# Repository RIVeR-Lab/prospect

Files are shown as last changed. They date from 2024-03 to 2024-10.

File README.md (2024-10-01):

# stewart_end_effector
Design and software for controlling a servo actuated stewart manipulator platform

Below is a description of and steps to run a Python script which accepts a desired pose of the Stewart platform and actuates six servos to attain that pose. The six servos must be connected via USB to the computer that is running the script, and the servos must each have a distinct ID from 1-6.

### compute_motor_angles.py:
Start a ROS service, /compute_motor_angles, which accepts the args x, y, z, psi, theta, phi (representing a desired pose of the top platform) and returns the corresponding motor angles (in radians) 
### move_to_motor_angles.py: 
A Python script which accepts the args x, y, z, psi, theta, phi (representing a desired pose of the top platform) and moves the Dynamixel servos to the required positions. Depends on the /compute_motor_angles service
### set_params.py: 
A Python script that sets the Stewart Platform parameters (i.e. crank arm length). Must be run before compute_motor_angles.py

## Example run:
1. roscore
1. rosrun set_params.py 
1. rosrun stewart_end_effector compute_motor_angles.py
1. rosrun move_to_motor_angles.py
1. rosservice call /stewart_control 5 20 95 0.1 0.2 0.3

### Troubleshooting:
1. Make sure all Dynamixel servos have unique IDs (from 1-6) through the Dynamixel Wizard ID inspection
1. move_to_motor_angles.py hardcodes information about the hardware. Double check that the information (especially the servo IDs and DEVICENAME) is correct 

### PROSPECT
Running the ur3e arm in conjunction with the kinect camera, and raster movement

ur_robot_driver can be installed from: https://github.com/UniversalRobots/Universal_Robots_ROS_Driver

ur3e_moveit_config can be installed from: http://wiki.ros.org/ur3_moveit_config

azure_kinect_ros_driver can be installed from: https://github.com/microsoft/Azure_Kinect_ROS_Driver/blob/melodic/docs/building.md

Configure host pc to be 192.168.0.86 subnet 255.255.255.0 default gateway 0.0.0.0
Configure robot pc to be 192.168.0.85

In different terminals, run the following commands: 

    roscore

    roslaunch ur_robot_driver ur3e_bringup.launch robot_ip:=192.168.0.85 kinematics_config:=$(rospack find stewart_end_effector)/config/robot_calibration.yaml

    #run rostest0 on the robot itself

    roslaunch ur3e_moveit_config moveit_planning_execution.launch

    roslaunch ur3e_moveit_config moveit_rviz.launch

    rosrun tf2_ros static_transform_publisher -0.2336 -0.152 0.774 1.57 1.57 -1.57 base_link camera_base

    roslaunch azure_kinect_ros_driver driver.launch overwrite_robot_model:=false rgb_point_cloud:=false depth_mode:=NFOV_UNBINNED 

    rosrun stewart_end_effector tof_triad.py

    roslaunch spectrometer_drivers ibsen.launch

    roslaunch stewart_end_effector master.launch

    python3 scripts/main.py

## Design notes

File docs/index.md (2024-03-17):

---
layout: default
title: Home
nav_order: 1
description: "PROSPECT"
permalink: /
---

# PROSPECT: Precision Robot Spectroscopy Exploration and Characterization Tool
**Nathaniel Hanson<sup>1,4,†,\*</sup>, Gary Lvov<sup>1,†</sup>, Vedant Rautela<sup>1</sup>, Samuel Hibbard<sup>>1</sup>, Ethan Holand<sup>1,3</sup>, Charles DiMarzio<sup>2</sup>, and Taşkın Padır<sup>1</sup>**

PROSPECT

## Abstract
Near Infrared (NIR) spectroscopy is widely used in industrial quality control and automation to test the purity and material quality of items. In this research, we propose a novel sensorized end effector and acquisition strategy to capture spectral signatures from objects and register them with a 3D point cloud. Our methodology first takes a 3D scan of an object generated by a time-of-flight depth camera and decomposes the object into a series of planned viewpoints covering the surface. We generate motion plans for a robot manipulator and end-effector to visit these viewpoints while maintaining a fixed distance and surface normal to ensure maximal spectral signal quality enabled by the spherical motion of the end-effector. By continuously acquiring surface reflectance values as the end-effector scans the target object, the autonomous system develops a four-dimensional model of the target object: position in an **R<sup>3</sup>** coordinate frame, and a wavelength vector denoting the associated spectral signature. We demonstrate this system in building spectral-spatial object profiles of increasingly complex geometries. As a point of comparison, we show our proposed system and spectral acquisition planning yields more consistent signal signals than naïve point scanning strategies for capturing spectral information over complex surface geometries. Our work represents a significant step towards high-resolution spectral-spatial sensor fusion for automated quality assessment.

- *†Equal Contribution; \*Corresponding author*
- *<sup>1</sup>Institute for Experiential Robotics*
- *<sup>2</sup>Electrical and Computer Engineering Department, Northeastern University, Boston, Massachusetts, USA.*
- *<sup>3</sup>Robotics Institute, Carnegie Mellon University, Pittsburgh, Pennsylvania, USA.*
- *<sup>4</sup>Lincoln Laboratory, Massachusetts Institute of Technology, Lexington, Massachusetts, USA.*

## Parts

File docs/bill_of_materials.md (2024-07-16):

---
layout: default
title: Bill of Materials
nav_order: 2
description: "Bill of materials for PROSPECT"
---

| BOM # | DESCRIPTION | QTY. | SUPPLIER | MATERIAL | PART NUMBER |
| ----- | --- | ---- | --- | --- | --- |
| 1 | [Bottom Platform](https://github.com/RIVeR-Lab/prospect/blob/main/CAD/STL/Bottom_Platform.STL) | 1 | CUSTOM PRINTED | ONYX | |
| 2 | [Crank Arm](https://github.com/RIVeR-Lab/prospect/blob/main/CAD/STL/Crank_Arm.STL) | 6 | CUSTOM PRINTED | ONYX | |
| 3 | [UR3 Adapter Plate](https://github.com/RIVeR-Lab/prospect/blob/main/CAD/STL/UR3_Adapter_Plate.STL) | 1 | CUSTOM PRINTED | ONYX | |
| 4 | [Top Platform](https://github.com/RIVeR-Lab/prospect/blob/main/CAD/STL/Top_Platform.STL) | 1 | CUSTOM PRINTED | ONYX | |
| 5 | [Top Platform Bottom Cover](https://github.com/RIVeR-Lab/prospect/blob/main/CAD/STL/Top_Platform_Bottom_Cover.STL) | 1 | CUSTOM PRINTED | ONYX | |
| 6 | [Electronics Enclosure](https://github.com/RIVeR-Lab/prospect/blob/main/CAD/STL/Electronics_Enclosure.STL) | 1 | CUSTOM PRINTED | ONYX | |
| 7 | [Electronics Lid](https://github.com/RIVeR-Lab/prospect/blob/main/CAD/STL/Electronics_Lid.STL) | 1 | CUSTOM PRINTED | ONYX | |
| 8 | [Electronics Enclosure Adapter](https://github.com/RIVeR-Lab/prospect/blob/main/CAD/STL/Electronics_Enclosure_Adapter.STL) | 3 | CUSTOM PRINTED | ONYX | |
| 9 | [Dynamixel XL,XC-330](https://www.robotis.us/dynamixel-xl330-m288-t/) | 6 | ROBOTIS | | XL330-M288-T |
| 10 | [Robotis U2D2](https://www.robotis.us/u2d2/) | 1 | ROBOTIS | | 902-0132-000 |
| 11 | [SMPS2Dynamixel](https://www.robotis.us/smps2dynamixel/) | 1 | ROBOTIS | | 902-0034-000 |
| 12 | [Adafruit QT Py-SAMD21](https://www.adafruit.com/product/4600) | 1 | Adafruit | | SAMD21 |
| 13 | [VL53L4CD TOF Sensor](https://www.adafruit.com/product/5396) | 3 | Adafruit | | VL53L4CD |
| 14 | [LIGHT BULBS](https://internationallight.com/instrumentation-and-sensor-light-sources/1896-t1-miniature-incandescent-ndir-lamp) | 3 | International Light Technologies | | 1150-9A LAMP 5V 115mA |
| 15 | [MOSFET](https://www.amazon.com/EEEEE-Transistors-Transistor-Assortment-Compartment/dp/B095NMT2SL) | 1 | Amazon | | BC517 |
| 16 | [Brass Screw-to-Expand Inserts](https://www.mcmaster.com/94510A030/) | 12 | McMaster-Carr | | 94510A030 |
| 17 | [Right Handed Oil-Embedded Ball Joint](https://www.mcmaster.com/6072K35/) | 6 | McMaster-Carr | | 6072K35 |
| 18 | [Left Handed Oil-Embedded Ball Joint](https://www.mcmaster.com/6072K351/) | 6 | McMaster-Carr | | 6072K351 |
| 19 | [Aluminum Unthreaded Spacer](https://www.mcmaster.com/92510A562/) | 12 | McMaster-Carr | | 92510A562 |
| 20 | [Aluminum Turnbuckle Connecting Rod](https://www.mcmaster.com/8420K171/) | 6 | McMaster-Carr | | 8420K171 |
| 21 | [Thread-Forming Screws M2x8](https://www.mcmaster.com/90380A327/) | 18 | McMaster-Carr | | 90380A327 |
| 22 | [Thread-Forming Screws M2x6](https://www.mcmaster.com/90380A326/) | 34 | McMaster-Carr | | 90380A326 |
| 23 | [Socket Head Cap Screw, M2x14](https://www.mcmaster.com/91290A045/) | 3 | McMaster-Carr | | 91290A045 |

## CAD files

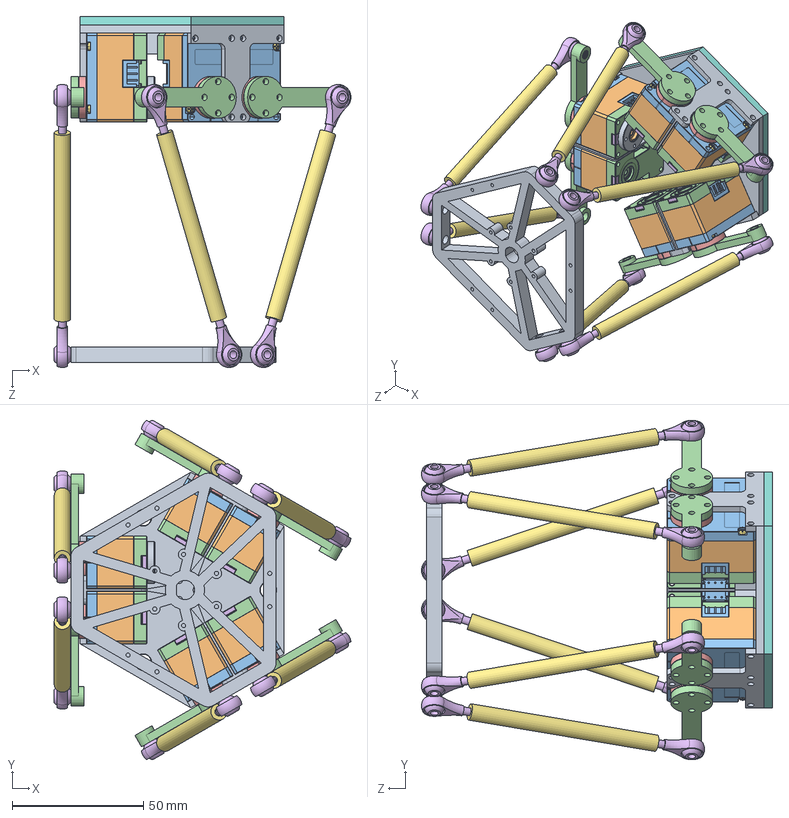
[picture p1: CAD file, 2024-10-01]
matlab/stewart_cad.SLDASM
113.2 x 129.3 x 133.8 mm
Bottom Platform_42023
DC15_A01_CASE_M_DUMMY.stp x 6
DC15_A01_CASE_F_DUMMY.stp x 6
DC15_A01_CASE_B_DUMMY.stp x 6
DC15_A01_HORN_DUMMY.stp x 6
DC15_A01_LED_CAP2_DUMMY.stp x 6
PHS_1_7X20_5_DC10.stp x 24
BTS2_M2_6X8.stp x 6
B3B-EH.stp x 12
SP, Crank Arm_42023 x 6
94510A030_Brass Screw-to-Expand Inserts_42023
59935K11_Ball Joint Rod End_42023 x 12
7415N11_Internally Threaded Connecting Rod_42023 x 6
Adapter Plate_42023
Top Platform 1_42023

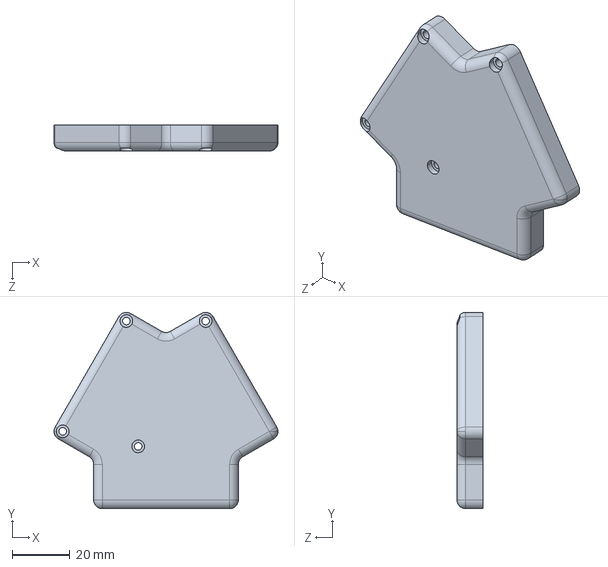
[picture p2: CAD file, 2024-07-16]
CAD/STEP/Electronics_Lid.STEP
77.4 x 67.8 x 9.00 mm

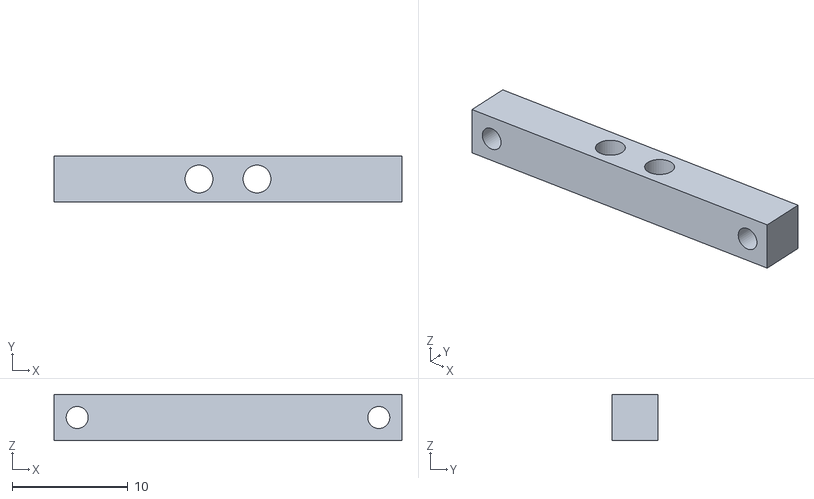
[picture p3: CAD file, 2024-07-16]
CAD/STL/Electronics_Enclosure_Adapter.STL
30.0 x 4.00 x 4.00

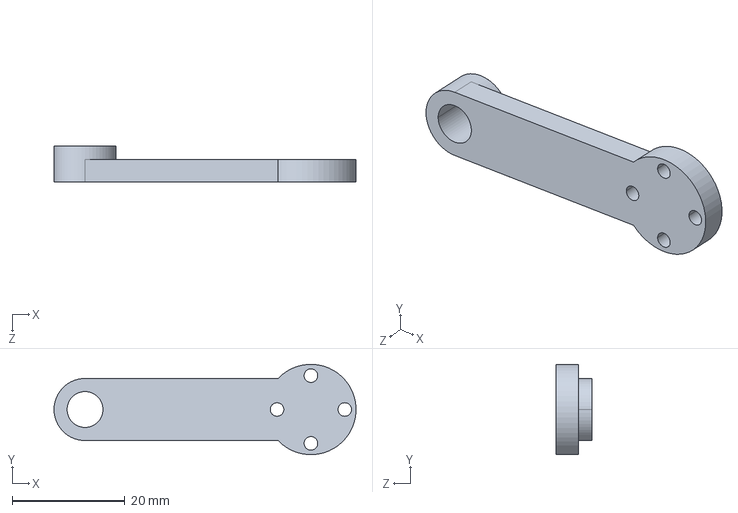
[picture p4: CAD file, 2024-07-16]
CAD/STEP/Crank_Arm.STEP
53.5 x 16.0 x 6.35 mm

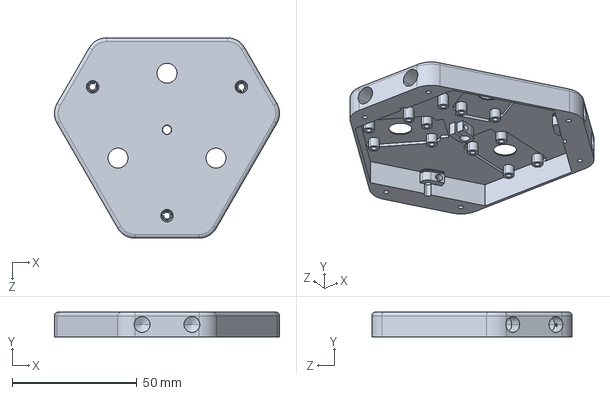
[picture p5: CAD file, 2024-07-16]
CAD/STEP/Top_Platform.STEP
90.3 x 10.0 x 80.4 mm

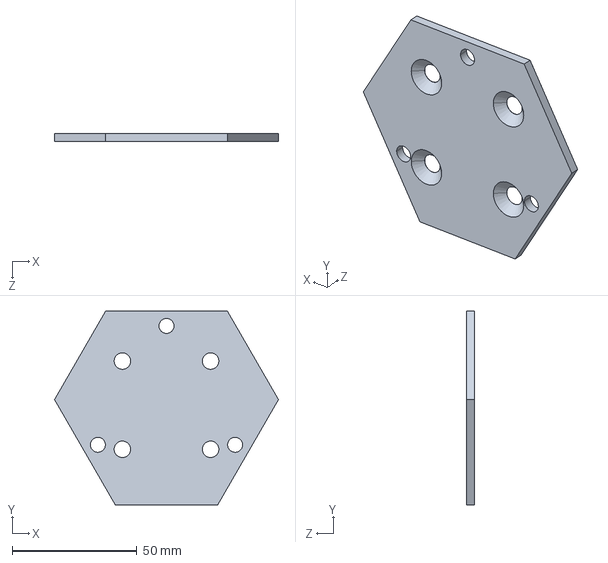
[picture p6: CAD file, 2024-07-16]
CAD/STEP/UR3_Adapter_Plate.STEP
89.8 x 77.8 x 3.30 mm

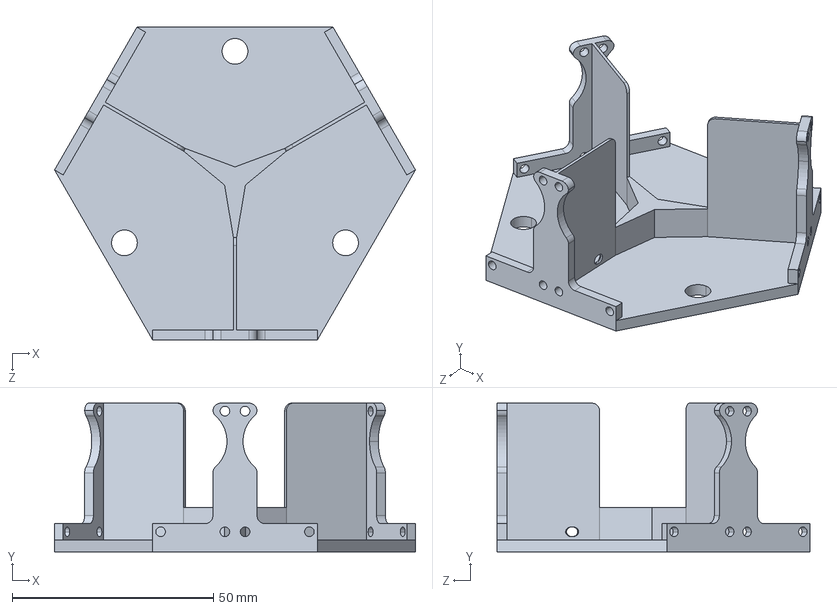
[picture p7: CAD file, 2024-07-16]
CAD/STEP/Bottom_Platform.STEP
89.8 x 37.0 x 77.8 mm

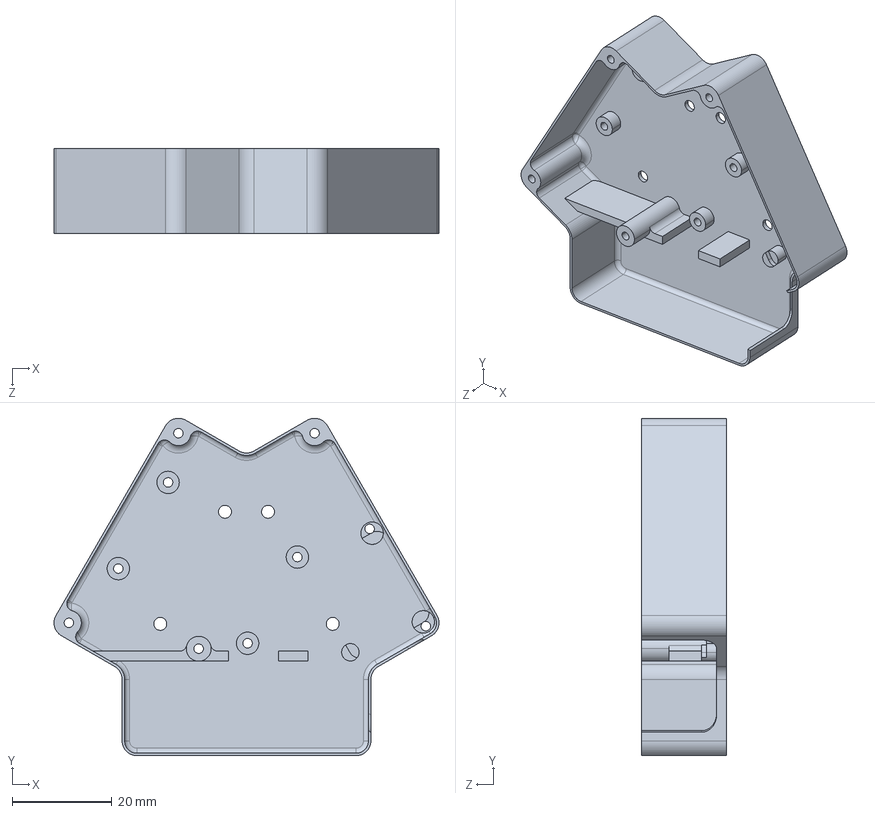
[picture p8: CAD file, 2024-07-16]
CAD/STEP/Electronics_Enclosure.STEP
77.4 x 67.8 x 17.1 mm

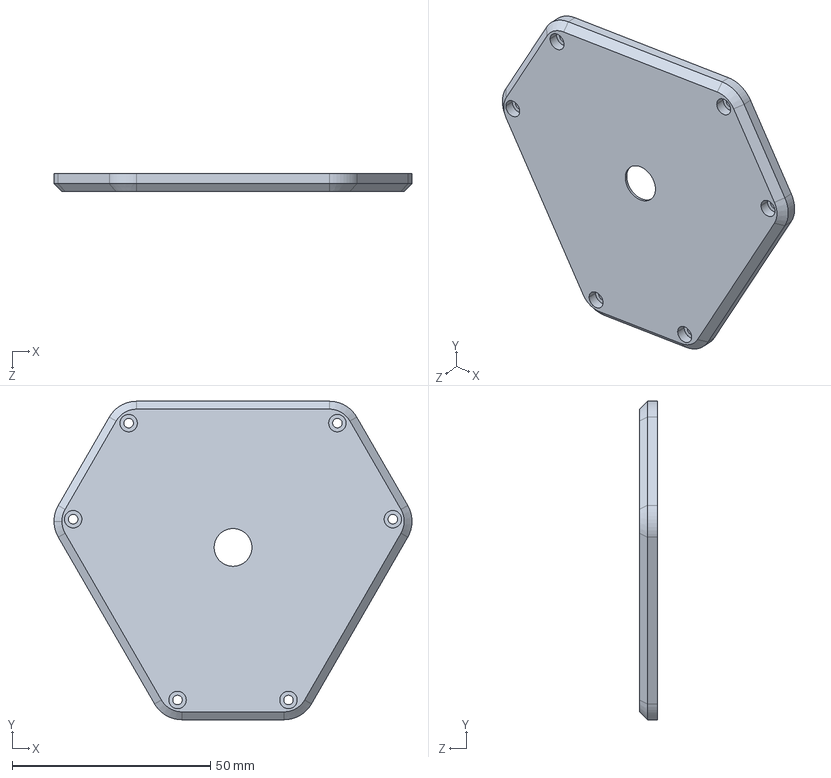
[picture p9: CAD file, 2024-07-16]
CAD/STEP/Top_Platform_Bottom_Cover.STEP
90.4 x 80.4 x 4.60 mm

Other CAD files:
CAD/STL/Bottom_Platform.STL
CAD/STL/Crank_Arm.STL
CAD/STL/Electronics_Enclosure.STL
CAD/STL/Electronics_Lid.STL
CAD/STL/Top_Platform.STL
CAD/STL/Top_Platform_Bottom_Cover.STL
CAD/STL/UR3_Adapter_Plate.STL

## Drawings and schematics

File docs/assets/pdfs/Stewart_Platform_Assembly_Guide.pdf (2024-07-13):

## 1: Final Assembled Model

4

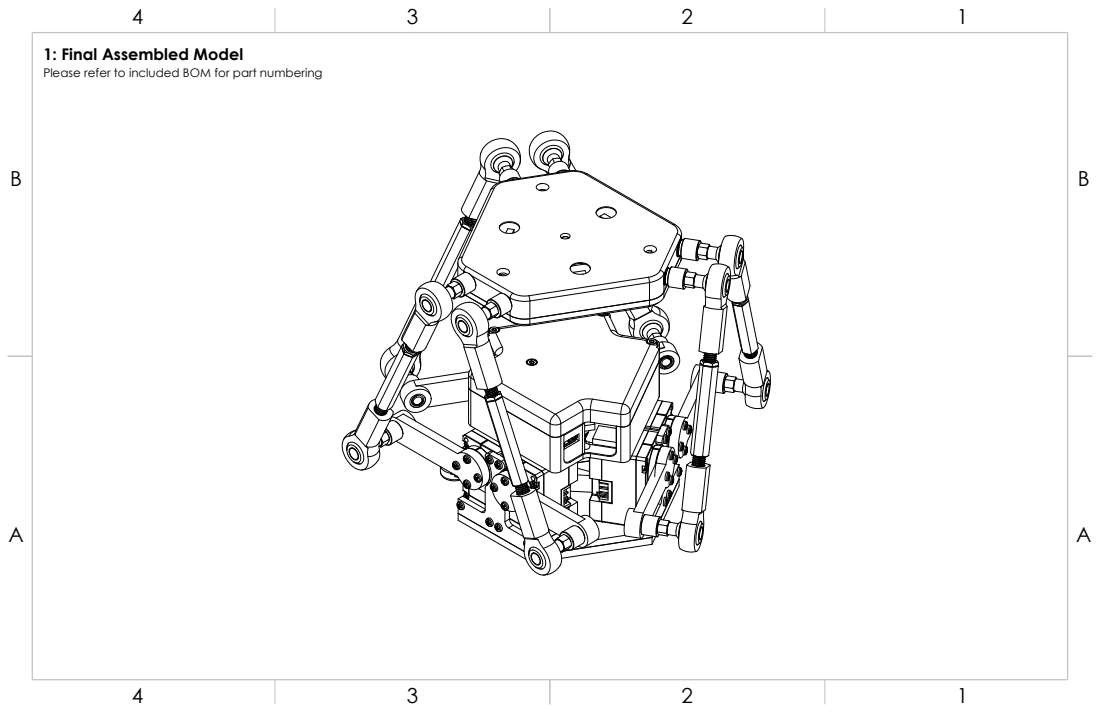
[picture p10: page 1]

Please refer to included BOM for part numbering

B B

## 2: Base Assembly

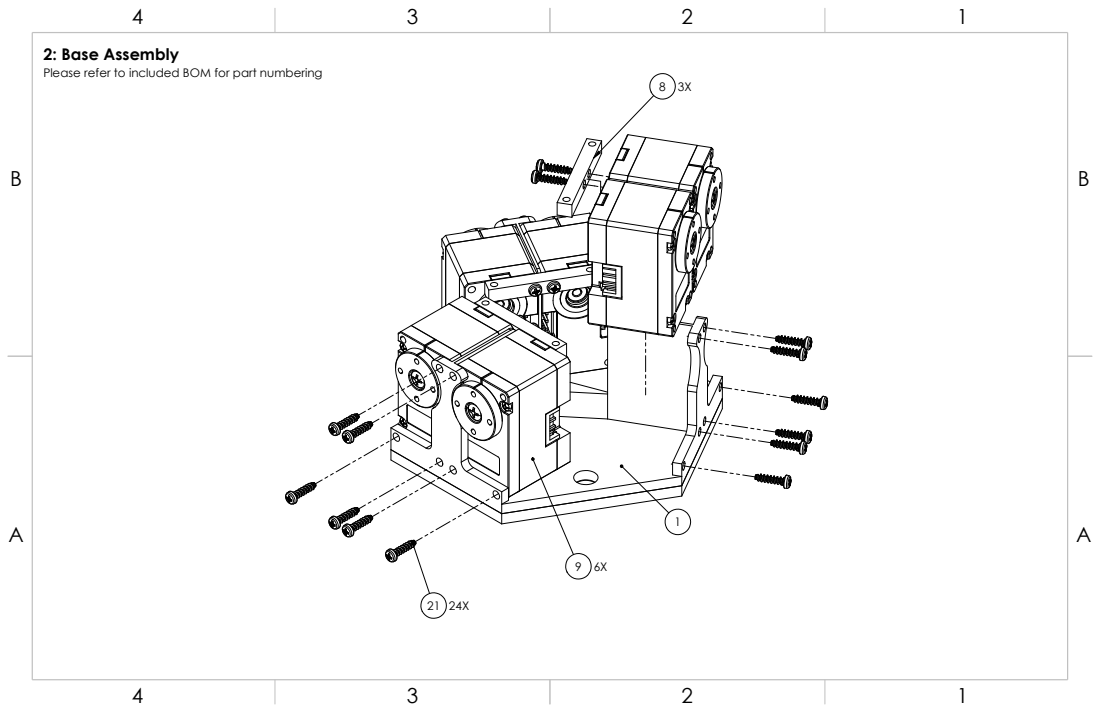
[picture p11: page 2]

Please refer to included BOM for part numbering

## 3: Crank Arms

B B

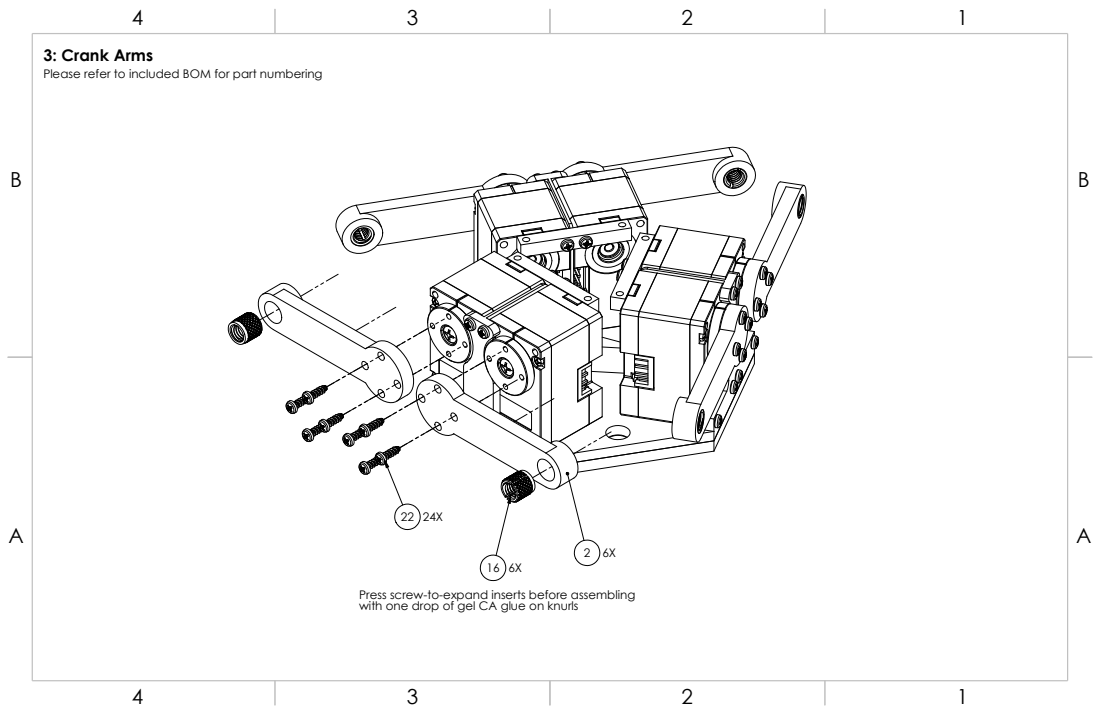
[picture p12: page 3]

Please refer to included BOM for part numbering

Press screw-to-expand inserts before assembling
with one drop of gel CA glue on knurls

B B

## 4: Electronics

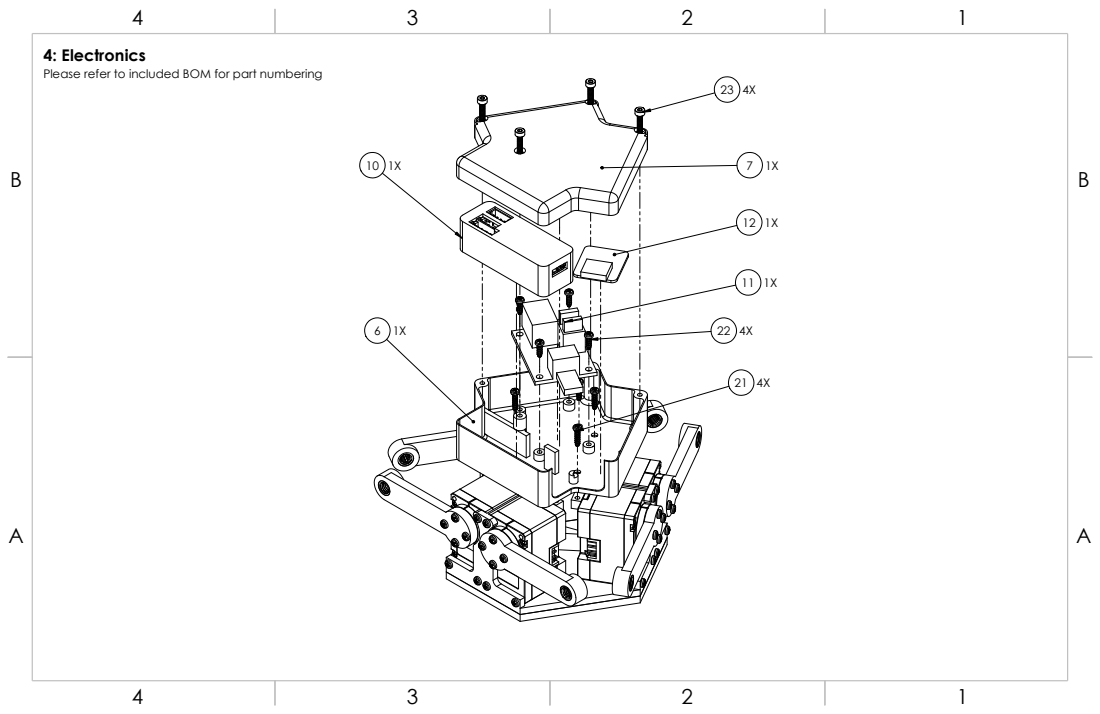
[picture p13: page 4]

Please refer to included BOM for part numbering

B B

## 5: Top Platform

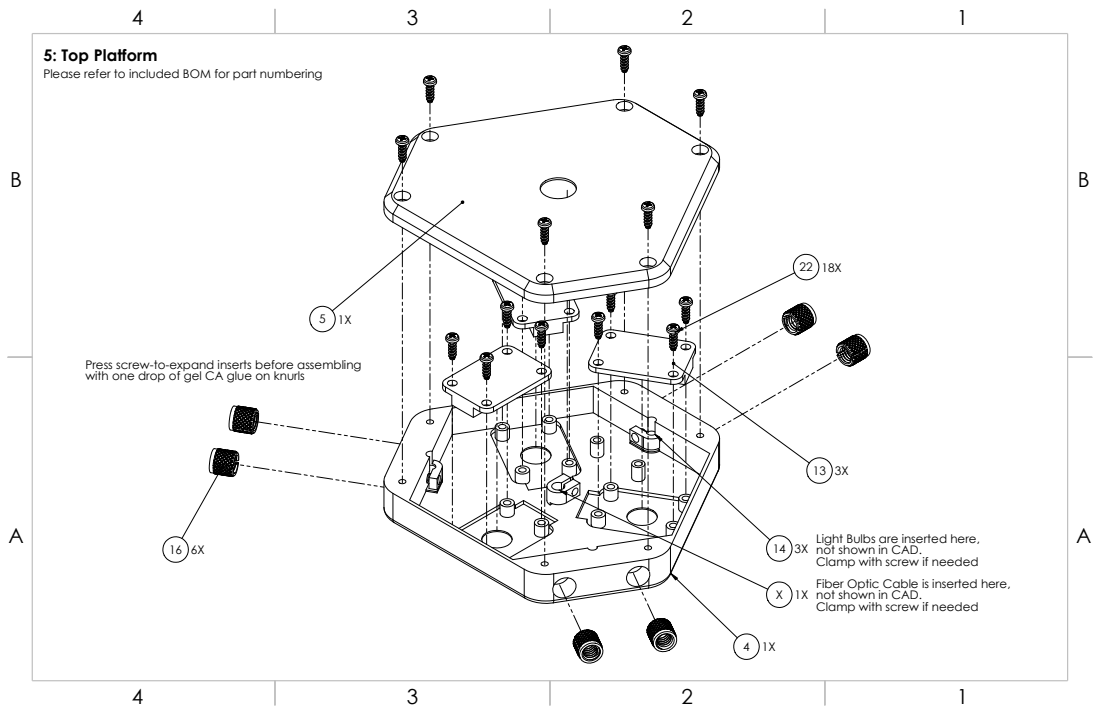
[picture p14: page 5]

Please refer to included BOM for part numbering

Press screw-to-expand inserts before assembling
with one drop of gel CA glue on knurls

Light Bulbs are inserted here,
not shown in CAD.
Clamp with screw if needed
Fiber Optic Cable is inserted here,

## 6: Links

B B

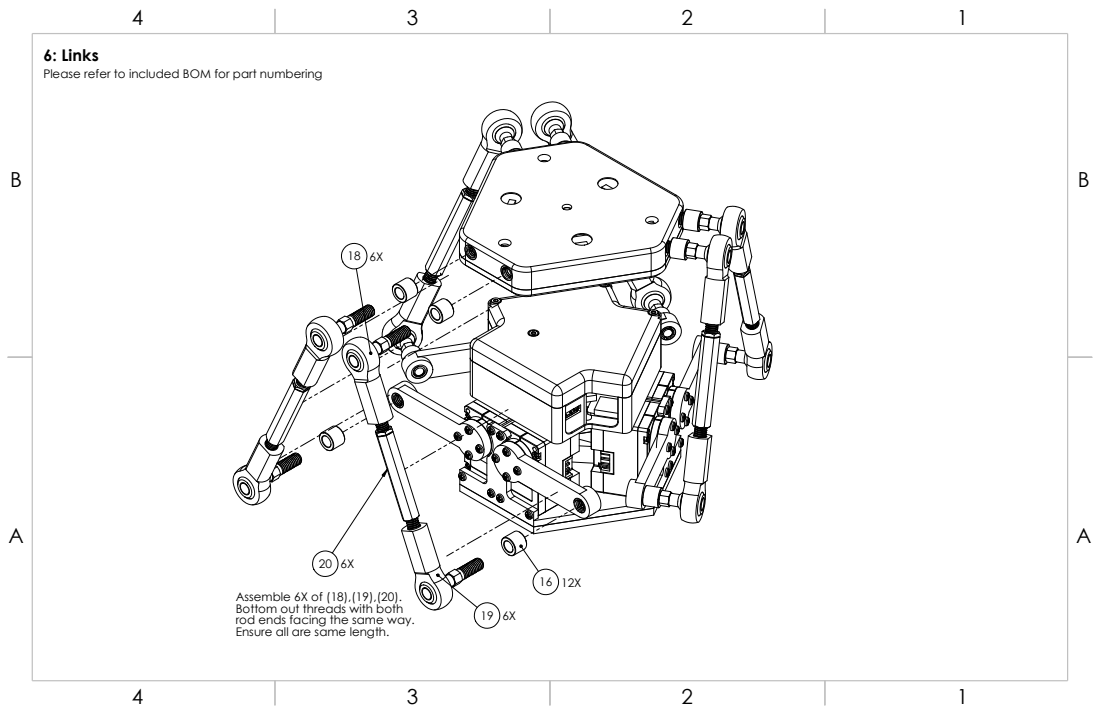
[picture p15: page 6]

Please refer to included BOM for part numbering

Assemble 6X of (18),(19),(20).
Bottom out threads with both
rod ends facing the same way.
Ensure all are same length.

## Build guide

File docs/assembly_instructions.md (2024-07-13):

---
layout: default
title: Assembly Instructions
nav_order: 3
description: "Assembly instructions for PROSPECT"
---

<iframe src="{{ site.baseurl }}/assets/pdfs/Stewart_Platform_Assembly_Guide.pdf" width="100%" height="600px">
    This browser does not support PDFs. Please download the PDF to view it: <a href="{{ site.baseurl }}/assets/pdfs/Stewart_Platform_Assembly_Guide.pdf">Download PDF</a>.
</iframe>

[Download PDF](assets/pdfs/Stewart_Platform_Assembly_Guide.pdf)

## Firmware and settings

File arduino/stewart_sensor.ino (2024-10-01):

#include <Wire.h>
#include "SparkFun_VL53L1X.h"

#define WIRE Wire
#define TCAADDR 0x70
//Optional interrupt and shutdown pins.
#define SHUTDOWN_PIN 2
#define INTERRUPT_PIN 3

SFEVL53L1X distanceSensor1;
SFEVL53L1X distanceSensor2;
SFEVL53L1X distanceSensor3;

// Helper function for changing TCA output channel
void tcaselect(uint8_t channel) {
  if (channel > 7) return;
  WIRE.beginTransmission(TCAADDR);
  WIRE.write(1 << channel);
  WIRE.endTransmission();  
}

void setup() {
  Serial.begin(9600);
  
  while (!Serial) {
     delay(10);
  }
  Serial.println("\nI2C Scanner");
  
  WIRE.begin();
  tcaselect(1);
  if (distanceSensor1.init() == false)
    Serial.println("Sensor #1 online!");
   tcaselect(6);
  if (distanceSensor2.init() == false)
    Serial.println("Sensor #2 online!"); 
  tcaselect(7);
  if (distanceSensor3.init() == false)
    Serial.println("Sensor #3 online!"); 
  pinMode(A0, OUTPUT);    // sets the digital pin 13 as output
  digitalWrite(A0, HIGH); // sets the digital pin 13 on
}


void find_devices() {
  byte error, address;
  int nDevices;
  Serial.println("Scanning...");
  nDevices = 0;
  for(address = 1; address < 127; address++ ) 
  {
    // The i2c_scanner uses the return value of
    // the Write.endTransmisstion to see if
    // a device did acknowledge to the address.
    WIRE.beginTransmission(address);
    error = WIRE.endTransmission();

    if (error == 0)
    {
      Serial.print("I2C device found at address 0x");
      if (address<16) 
        Serial.print("0");
      Serial.print(address,HEX);
      Serial.println("  !");

      nDevices++;
    }
    else if (error==4) 
    {
      Serial.print("Unknown error at address 0x");
      if (address<16) 
        Serial.print("0");
      Serial.println(address,HEX);
    }    
  }
  if (nDevices == 0)
    Serial.println("No I2C devices found\n");
  else
    Serial.println("done\n");
}

void readSerial() {
  String str = Serial.readString();
  // Check string is non-empty
  if (str.length() < 3){
    return;
  }
  // Set light value
  if (str.indexOf("light_power") > -1) {
    // Set light equal to the power value
    int offset = 12; // Number of characters until useful data begins
    String command = str.substring(offset);
    command.trim();
    if (command.equals("ON")) {
      digitalWrite(A0, LOW); 
    } else if (command.equals("OFF")) {
      digitalWrite(A0, HIGH); 
    }
    return;
  }
//  // Set integration time
//  if (str.indexOf("integration_time") > -1) {
//    // Extract the integration time to use
//    // Set light equal to the power value
//    int offset = 16; // Number of characters until useful data begins
//    String command = str.substring(offset);
//    command.trim();
//    // Convert string to integer value
//    int newTime = command.toInt();
//    delayTime = newTime;
//  }
}

void loop() {
//  Serial.println("Checking index 0");
  tcaselect(1);
  distanceSensor1.startRanging(); //Write configuration bytes to initiate measurement
  int distance1 = distanceSensor1.getDistance(); //Get the result of the measurement from the sensor
  distanceSensor1.stopRanging();
//  Serial.println("Checking index 1");
  tcaselect(6);
  distanceSensor2.startRanging(); //Write configuration bytes to initiate measurement
  int distance2 = distanceSensor2.getDistance(); //Get the result of the measurement from the sensor
  distanceSensor2.stopRanging();
//  Serial.println("Checking index 2");
  tcaselect(7);
  distanceSensor3.startRanging(); //Write configuration bytes to initiate measurement
  int distance3 = distanceSensor3.getDistance(); //Get the result of the measurement from the sensor
  distanceSensor3.stopRanging();
  Serial.print("Distance 1 (mm): ");
  Serial.print(distance1);
  Serial.print(", Distance 2 (mm): ");
  Serial.print(distance2);
  Serial.print(", Distance 3 (mm): ");
  Serial.print(distance3);
  Serial.println();
//  digitalWrite(A0, HIGH); // sets the digital pin 13 on
  //delay(100);          // wait 10 milliseconds for the next scan
//  digitalWrite(A0, LOW); // sets the digital pin 13 on
  //delay(100);          // wait 10 milliseconds for the next scan
  delay(10);
  readSerial();

}

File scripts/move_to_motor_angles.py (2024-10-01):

#!/usr/bin/env python3

import numpy as np
import os
import rospy
import sys
from threading import Lock
from std_msgs.msg import Float32MultiArray
from stewart_end_effector.srv import StewartControl, ComputeMotorAngles, ComputeMotorAnglesResponse
from compute_motor_angles import normalize_motor_angles_zero_twopi, normalize_motor_angles_pi_minus_pi
from stewart_end_effector.srv import StewartControl, StewartControlRequest, StewartControlResponse


if os.name == 'nt':
    import msvcrt
    def getch():
        return msvcrt.getch().decode()
else:
    import sys, tty, termios
    fd = sys.stdin.fileno()
    old_settings = termios.tcgetattr(fd)
    def getch():
        try:
            tty.setraw(sys.stdin.fileno())
            ch = sys.stdin.read(1)
        finally:
            termios.tcsetattr(fd, termios.TCSADRAIN, old_settings)
        return ch


from dynamixel_sdk.port_handler import PortHandler # goes into the port_handler.py file and imports the class PortHandler
from dynamixel_sdk.packet_handler import PacketHandler # does the same as the previous line but PacketHandler is a function
from dynamixel_sdk.group_sync_write import GroupSyncWrite
from dynamixel_sdk.group_sync_read import GroupSyncRead
from dynamixel_sdk.robotis_def import *
import dynamixel_sdk as dxl

#********* DYNAMIXEL Model definition *********
#***** (Use only one definition at a time) *****
MY_DXL = 'X_SERIES'       # X330 (5.0 V recommended), X430, X540, 2X430
# Control table address
if MY_DXL == 'X_SERIES' or MY_DXL == 'MX_SERIES':
    ADDR_TORQUE_ENABLE          = 64
    ADDR_GOAL_POSITION          = 116
    LEN_GOAL_POSITION           = 4         # Data Byte Length
    ADDR_PRESENT_POSITION       = 132
    LEN_PRESENT_POSITION        = 4         # Data Byte Length
    ADDR_HARDWARE_ERROR              = 70
    LEN_HARDWARE_ERROR          = 1
    DXL_MINIMUM_POSITION_VALUE  = 0         # Refer to the Minimum Position Limit of product eManual
    DXL_MAXIMUM_POSITION_VALUE  = 4095      # Refer to the Maximum Position Limit of product eManual
    BAUDRATE                    = 57600

# DYNAMIXEL Protocol Version (1.0 / 2.0)
# https://emanual.robotis.com/docs/en/dxl/protocol2/
PROTOCOL_VERSION            = 2.0

# Make sure that each DYNAMIXEL ID should have unique ID.
DXL1_ID                     = 1                 # Dynamixel#1 ID : 1
DXL2_ID                     = 2                 # Dynamixel#1 ID : 2
DXL3_ID                     = 3                 # Dynamixel#1 ID : 3
DXL4_ID                     = 4                 # Dynamixel#1 ID : 4
DXL5_ID                     = 5                 # Dynamixel#1 ID : 5
DXL6_ID                     = 6                 # Dynamixel#1 ID : 6

DXL_IDS = [DXL1_ID, DXL2_ID, DXL3_ID, DXL4_ID, DXL5_ID, DXL6_ID]

# Use the actual port assigned to the U2D2.
# ex) Windows: "COM*", Linux: "/dev/ttyUSB*", Mac: "/dev/tty.usbserial-*"
DEVICENAME                  = '/dev/output/stewart-motor'

TORQUE_ENABLE               = 1                 # Value for enabling the torque
TORQUE_DISABLE              = 0                 # Value for disabling the torque
DXL_MOVING_STATUS_THRESHOLD = 20                # Dynamixel moving status threshold

DEGREE_TO_POSITION_VALUE = (DXL_MAXIMUM_POSITION_VALUE - DXL_MINIMUM_POSITION_VALUE)/360.0


class MoveMotorAngles():
    def __init__(self):
        # Initialize PortHandler instance
        # Set the port path
        # Get methods and members of PortHandlerLinux or PortHandlerWindows
        self.portHandler = PortHandler(DEVICENAME)

        # Initialize PacketHandler instance
        # Set the protocol version
        # Get methods and members of Protocol1PacketHandler or Protocol2PacketHandler
        self.packetHandler = PacketHandler(PROTOCOL_VERSION)

        # Initialize GroupSyncWrite instance
        self.groupSyncWrite = GroupSyncWrite(self.portHandler, self.packetHandler, ADDR_GOAL_POSITION, LEN_GOAL_POSITION)

        # Initialize GroupSyncRead instance for Present Position
        self.groupSyncRead = GroupSyncRead(self.portHandler, self.packetHandler, ADDR_PRESENT_POSITION, LEN_PRESENT_POSITION)
        self.groupSyncReadAlarm = GroupSyncRead(self.portHandler, self.packetHandler, ADDR_HARDWARE_ERROR, LEN_HARDWARE_ERROR)

        self.pub = rospy.Publisher('actual_motor_positions', Float32MultiArray, queue_size=1)
        self.pub_srv_lock = Lock()

    
    def initialize(self):
        # Open port
        if self.portHandler.openPort():
            print("Succeeded to open the port")
        else:
            print("Failed to open the port")
            print("Press any key to terminate...")
            getch()
            quit()

        # Set port baudrate
        if self.portHandler.setBaudRate(BAUDRATE):
            print("Succeeded to change the baudrate")
        else:
            print("Failed to change the baudrate")
            print("Press any key to terminate...")
            getch()
            quit()

    
    def zero_platform(self):
        '''
        Zero the platform to start
        '''
        rospy.sleep(3)
        cmd = StewartControl()
        cmd.x, cmd.y, cmd.z, cmd.psi, cmd.theta, cmd.phi = 0, 0, 100, 0, 0, 0
        self.compute_motor_angles_client(cmd)

    # Initialize each of the servos with certain parameters
    def boot_servo(self, dxl_id):
        # TODO: ensure that torque does not need to be enabled when booting servos since auto-enable was set in the Dynamixel Wizard
        # Enable torques for each of the Dynamixels
        dxl_comm_result, dxl_error = self.packetHandler.write1ByteTxRx(self.portHandler, dxl_id, ADDR_TORQUE_ENABLE, TORQUE_ENABLE)
        if dxl_comm_result != COMM_SUCCESS:
            print("NO COMM SUCCESS")
            print(dxl_comm_result)
            print("%s" % self.packetHandler.getTxRxResult(dxl_comm_result))
        elif dxl_error != 0:
            print("DXL ERROR")
            print("%s" % self.packetHandler.getRxPacketError(dxl_error))
        else:
            print("Dynamixel#%d has been successfully connected" % dxl_id)

        ADDR_PROFILE_VELOCITY = 112
        DESIRED_MAX_VELOCITY = 30
        self.set_servo_param(dxl_id, 'profile velocity', 4, ADDR_PROFILE_VELOCITY, DESIRED_MAX_VELOCITY)

        ADDR_POSITION_D_GAIN = 80
        DESIRED_POSITION_D_GAIN = 0
        self.set_servo_param(dxl_id, 'position D gain', 2, ADDR_POSITION_D_GAIN, DESIRED_POSITION_D_GAIN)

        ADDR_POSITION_I_GAIN = 82
        DESIRED_POSITION_I_GAIN = 250
        self.set_servo_param(dxl_id, 'position I gain', 2, ADDR_POSITION_I_GAIN, DESIRED_POSITION_I_GAIN)

        ADDR_POSITION_P_GAIN = 84
        DESIRED_POSITION_P_GAIN = 500
        self.set_servo_param(dxl_id, 'position P gain', 2, ADDR_POSITION_P_GAIN, DESIRED_POSITION_P_GAIN)
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

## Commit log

2024-07-02 Added CAD files
    [Bottom_Platform.STL, Crank_Arm.STL, Electronics_Enclosure_Adapter.STL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]
2024-07-02 Renamed STL Files and added links to BOM
    [Stewart_Electronics_Enclosure_Lid.STL, Top_Platform_Bottom_Cover.STL]
2024-07-02 Update bill_of_materials.md
    Corrected STL Links
2024-07-13 try to add embed assembly instructions pdf
2024-07-14 Update bill_of_materials.md
    Add BOM # and reformat links
2024-07-16 Added STEP models and updated STLs
    [Bottom_Platform.STEP, Bottom_Platform.STL, Crank_Arm.STEP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]
2024-10-01 everything (#3)
    [robot_calibration.yaml, stewart_cad.SLDASM]
